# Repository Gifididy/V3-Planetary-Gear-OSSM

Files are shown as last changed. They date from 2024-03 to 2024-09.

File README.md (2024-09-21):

# V3-Planetary-Gear-OSSM
My take on an OSSM variant using a planetary gear set to increase torque while still using the core hardware of the original OSSM. An easy fix for if the OSSM does not have enough torque/force for you. 

## Hardware

Hex cap metric screws

3 x M3x12 - Endstops

7 x M3x8 - Rack

1 x M4x8 - Set screw for spindle gear 

10 x M4x16 - Used for connecting motor mount & 2 pin mount to the top bracket

6 x M4x12 - For mounting to a plywood base. May need to be longer depending on the mounting method. I used m4 threaded inserts for wood. 

10 x M4x8 - Linear rail & Rack

4 x M5x16 - Gear bearing screws

4 x M5x25 - Motor mount bolts

5x M4x5.5mm wide threaded inserts - Set into top bracket and spindle gear set screw. 

10 x M3 nuts

6 x M4 nuts

4 x M5 nuts

------

2 x 8mm dowels - Each 85mm or longer.

4x 685ZZ Bearings - Same ones OSSM uses.

1 x MGN12H Linear rail - Same style OSSM uses. I'm using a 400mm one currently.

180W servo - Recommended OSSM one.

OSSM control board and remote - **Will need to modify software. Just a couple values need to be changed.**

Appropriate power supply.

# Changes to code

**utilities.cpp**

Line 481 value changed to 2

**pattern.h**

I disabled line 850 and 851 because those sucked to accidently switch to.

**OSSM_Config.h**

line 32 from 900 to 50 (Lowers max speed but also gives more low speed range and options. Increase value if you want higher top speed)

line 37 from 20 to 4 (This is how I'm telling the software I'm using a gear reduciton)

Optional

line 60 from 6 to 4 (Less dead space from homing. Gives a little bit more useable distance)

~~line 65 from 100 to 1000 (More smoothly transitions directions)~~ Found this to cause the servo to stop moving at lower speeds which is what causes over current protection. 

## Printed parts notes

Note on some of the printer settings I use.

Nozzle: .6mm

Layer height: .3mm

Wall, top & bottom thickness: 1.2mm

Infill: 30% - cubic

Some support is needed for the planet carrier and the top motor mount that has the planet carrier bearing screw. Depending on your settings, you may be able to not use any support material at all. 

Should use less than a spool of filament. I've been using PLA for reference. 

"2 Pin bracket" is the height-adjust bracket that can be mounted to a piece of plywood or other available large flat surface. Will need to print two of these. This version is symmetric and does not need to be mirrored.

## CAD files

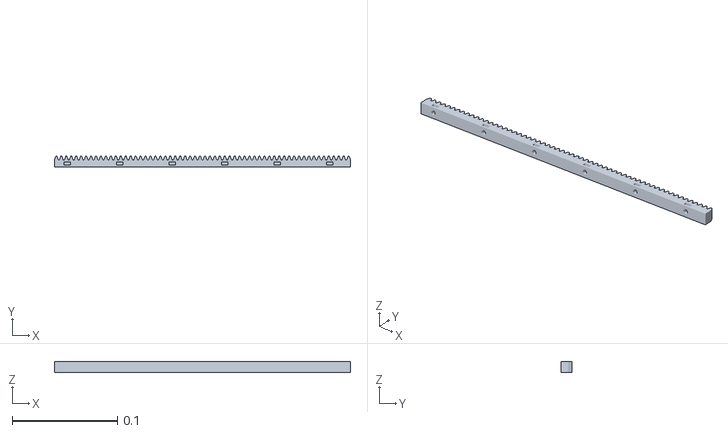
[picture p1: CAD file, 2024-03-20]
V3 Gear Driven Planetary/Rack.stl
0.282 x 0.01 x 0.01

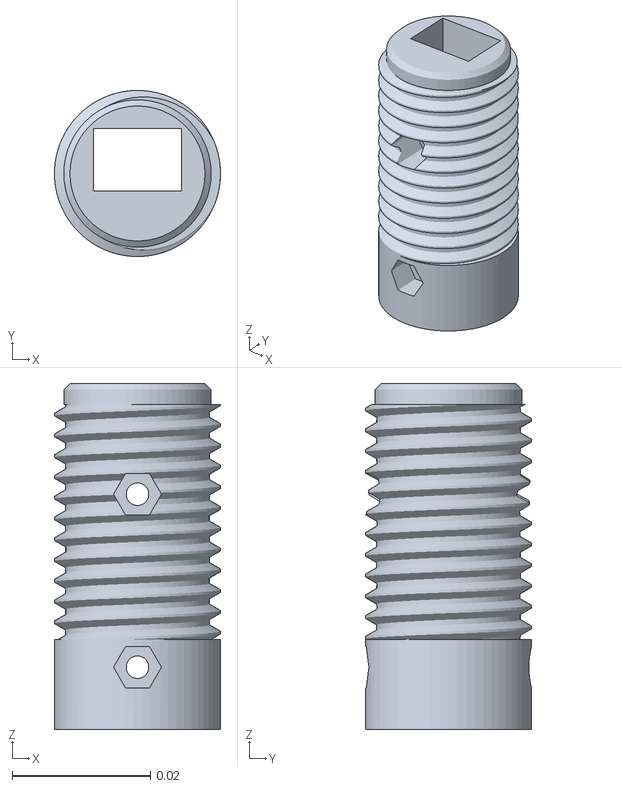
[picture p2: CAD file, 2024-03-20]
V3 Gear Driven Planetary/Toy Mount Endstop.stl
0.024 x 0.024 x 0.05

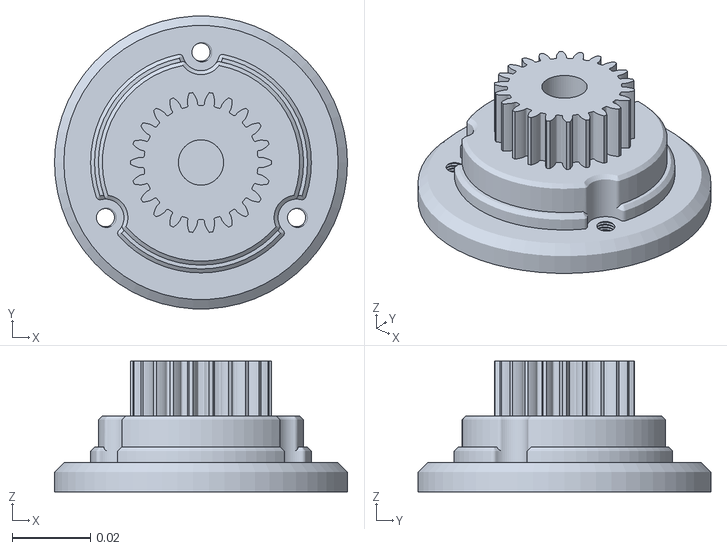
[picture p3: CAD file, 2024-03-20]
V3 Gear Driven Planetary/Alt Planet Carrier Slimmed.stl
0.075 x 0.0749 x 0.0335

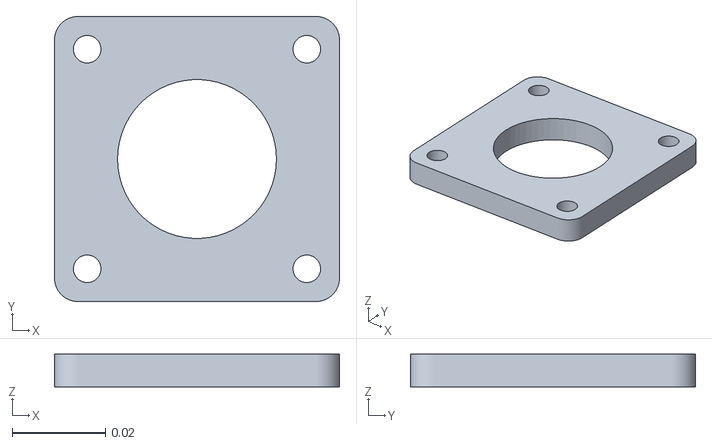
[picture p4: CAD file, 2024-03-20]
V3 Gear Driven Planetary/Motor Spacer.stl
0.061 x 0.061 x 0.007

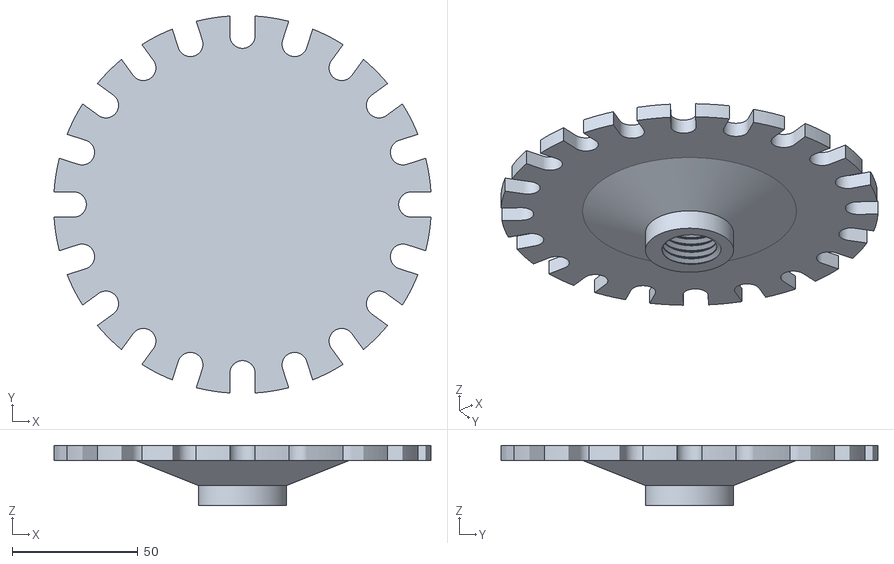
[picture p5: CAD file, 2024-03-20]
V3 Gear Driven Planetary/Flat End Effector Large.stl
149.7 x 149.7 x 24.0

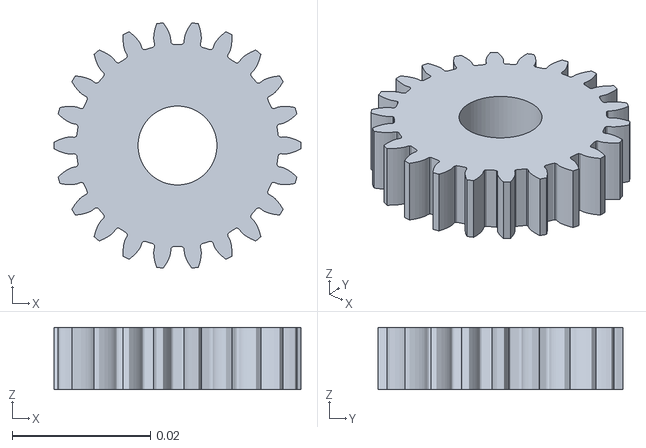
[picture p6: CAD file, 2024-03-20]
V3 Gear Driven Planetary/22T Planet Gear.stl
0.0357 x 0.0355 x 0.009

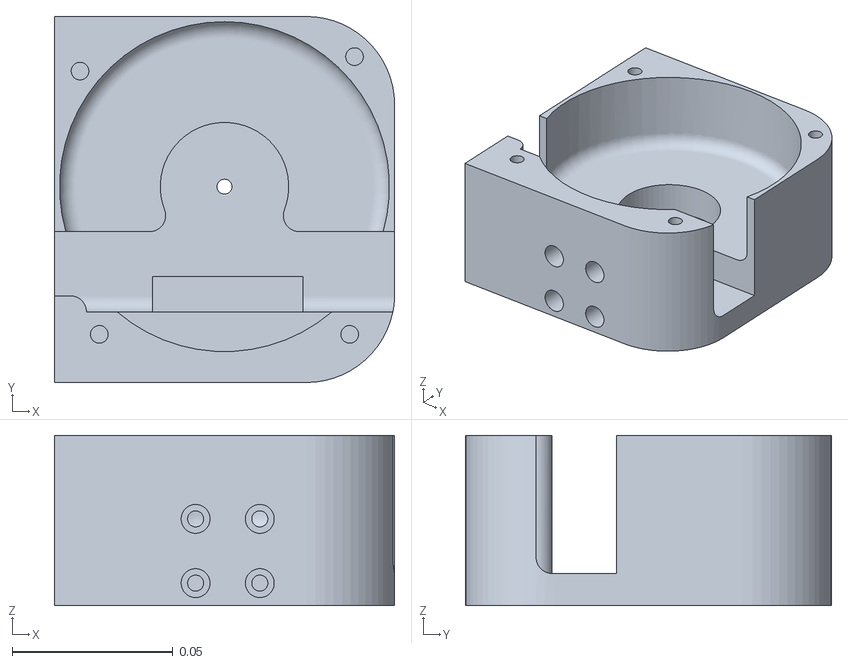
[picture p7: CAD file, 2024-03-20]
V3 Gear Driven Planetary/Top Bracket.stl
0.106 x 0.114 x 0.053

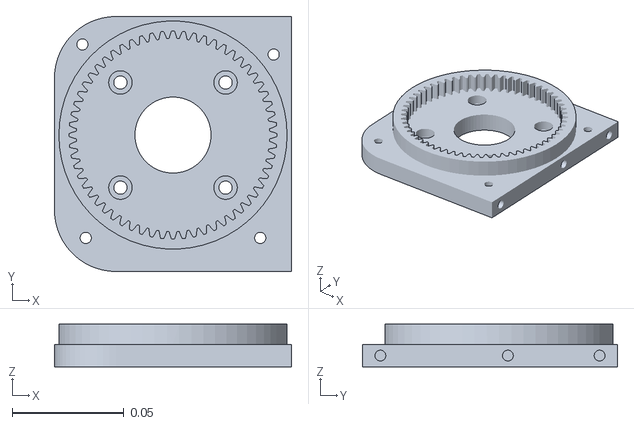
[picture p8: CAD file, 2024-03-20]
V3 Gear Driven Planetary/Motor Mount.stl
0.106 x 0.114 x 0.019

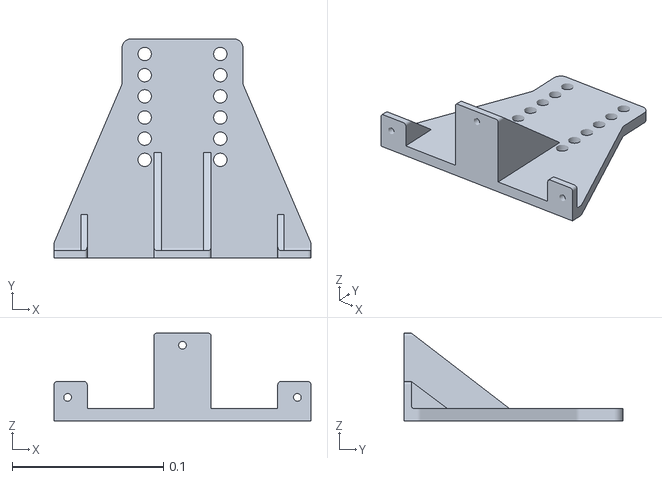
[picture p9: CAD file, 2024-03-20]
V3 Gear Driven Planetary/2 Pin Bracket.stl
0.17 x 0.145 x 0.058

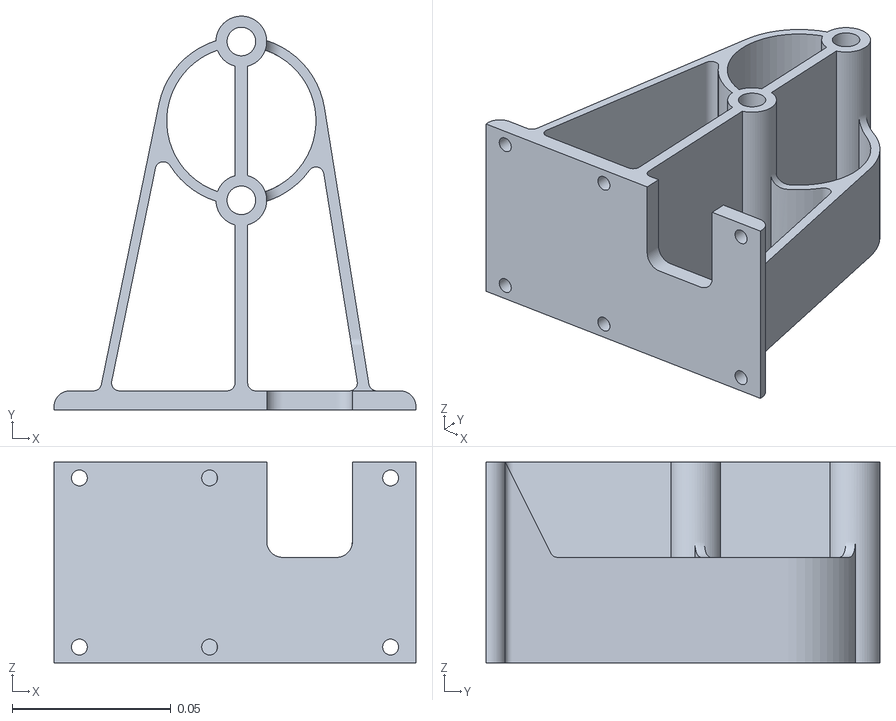
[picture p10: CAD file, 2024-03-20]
V3 Gear Driven Planetary/2 Pin Mount.stl
0.114 x 0.124 x 0.0632

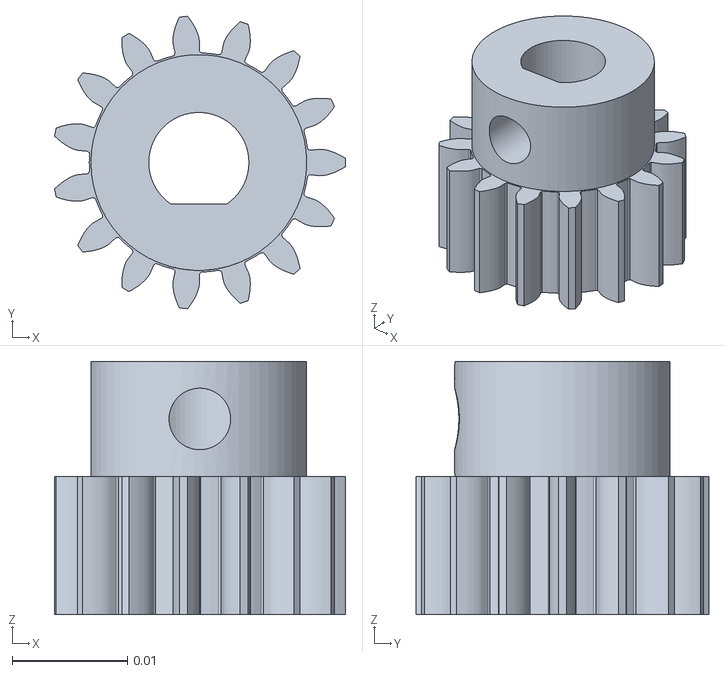
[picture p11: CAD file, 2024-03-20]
V3 Gear Driven Planetary/Alt Spindle Gear.stl
0.0253 x 0.0254 x 0.022

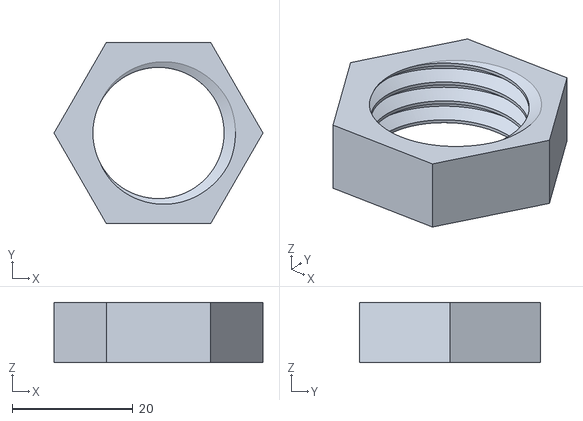
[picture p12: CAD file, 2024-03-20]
V3 Gear Driven Planetary/Jam Nutt.stl
34.6 x 30.0 x 10.0

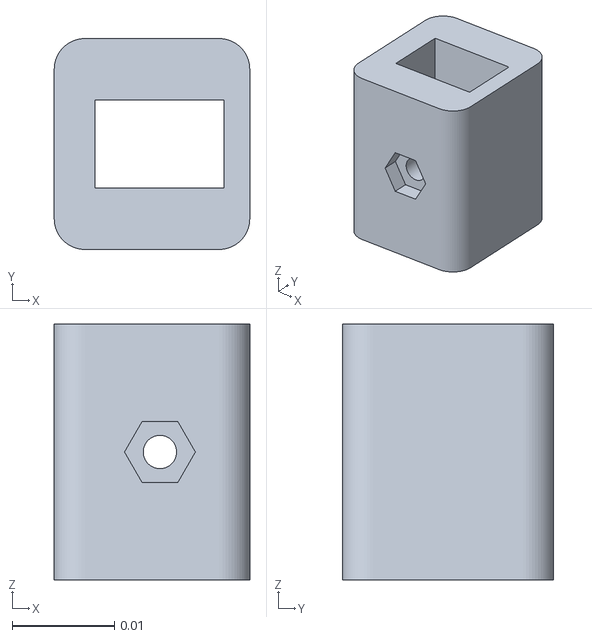
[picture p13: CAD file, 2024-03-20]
V3 Gear Driven Planetary/Rear Endstop.stl
0.0191 x 0.0206 x 0.025

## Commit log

2024-04-05 Update README.md
    Changed software values to better account for gear reduction system and high speed issues.
2024-09-21 Update README.md
    Strike though and note for like 65 causing over current protection
